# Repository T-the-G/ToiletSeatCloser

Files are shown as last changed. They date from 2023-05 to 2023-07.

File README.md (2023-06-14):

# Toilet Seat Closer

<figure>
  Timelapse of the toilet seat closer, the entire action takes about 2.5 minutes
</figure>
Lever that closes the toilet seat 

# Table of Contents  

- [Gallery](#gallery)
- [How it works](#how-it-works)
- [Bill of Materials](#bill-of-materials)  
  - [3D-printed parts](#3d-printed-parts)  
  - [Electronics](#electronics)
  - [Fasteners and other mechanical parts](#fasteners-and-other-mechanical-parts)
- [Future improvements](#future-improvements)

# Gallery

<p float="left">
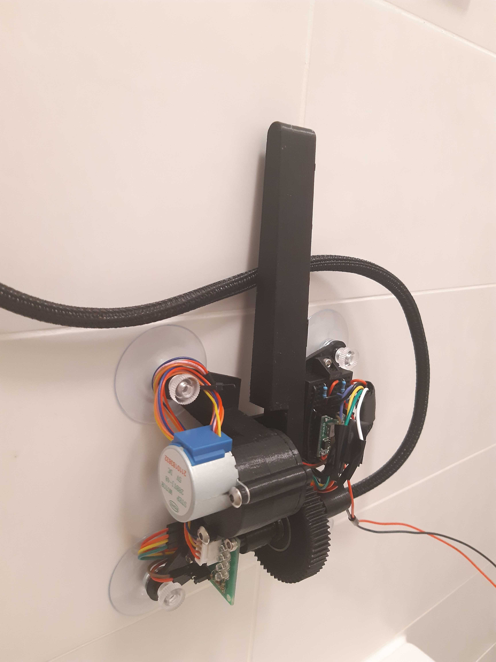
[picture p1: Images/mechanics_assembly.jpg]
  
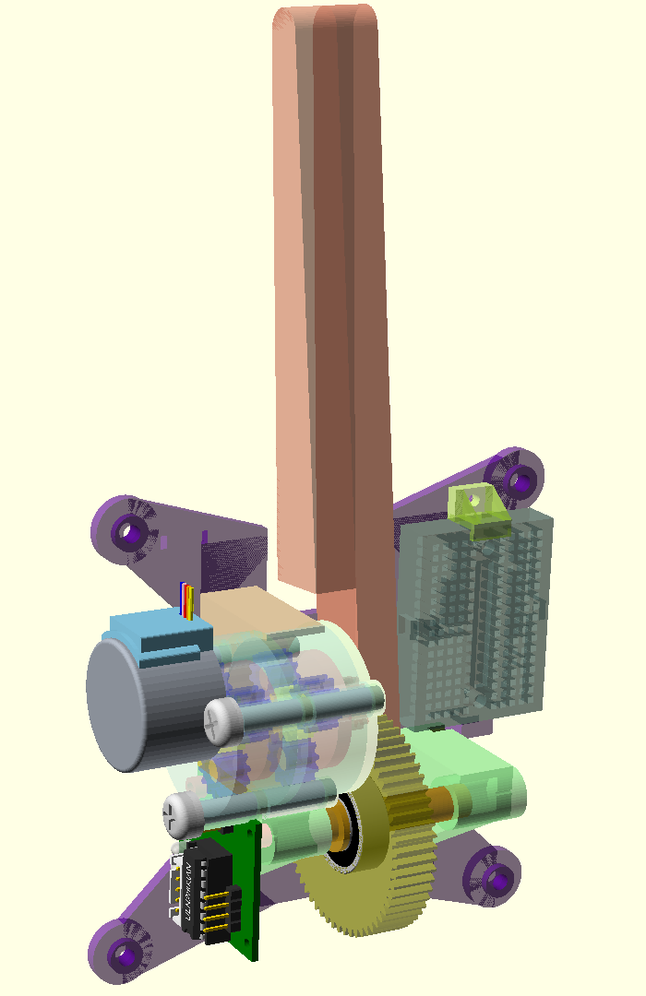
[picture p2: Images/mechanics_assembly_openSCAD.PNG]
   
</p>
Mechanics assembly

---

<p float="left">
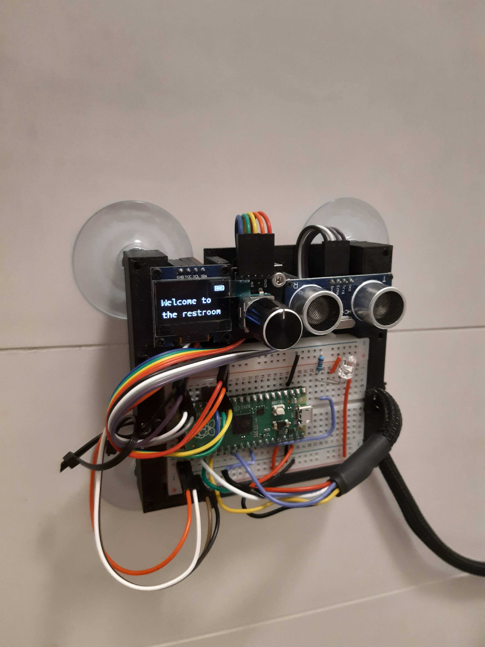
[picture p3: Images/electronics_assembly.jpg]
  
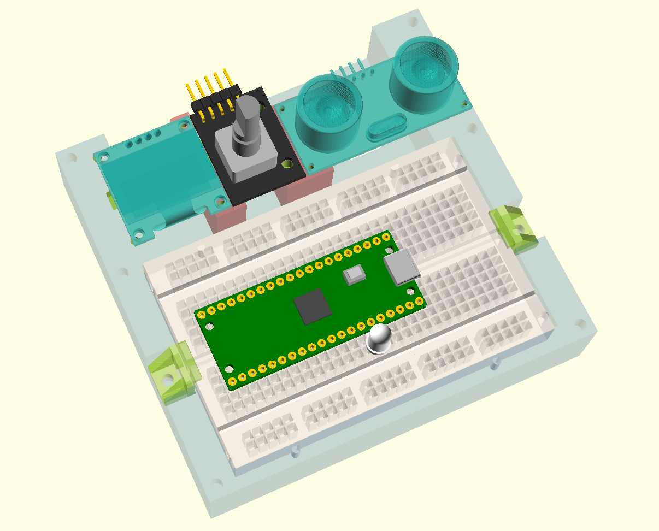
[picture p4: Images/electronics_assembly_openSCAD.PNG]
   
</p>
Electronics assembly

---

<p float="left">
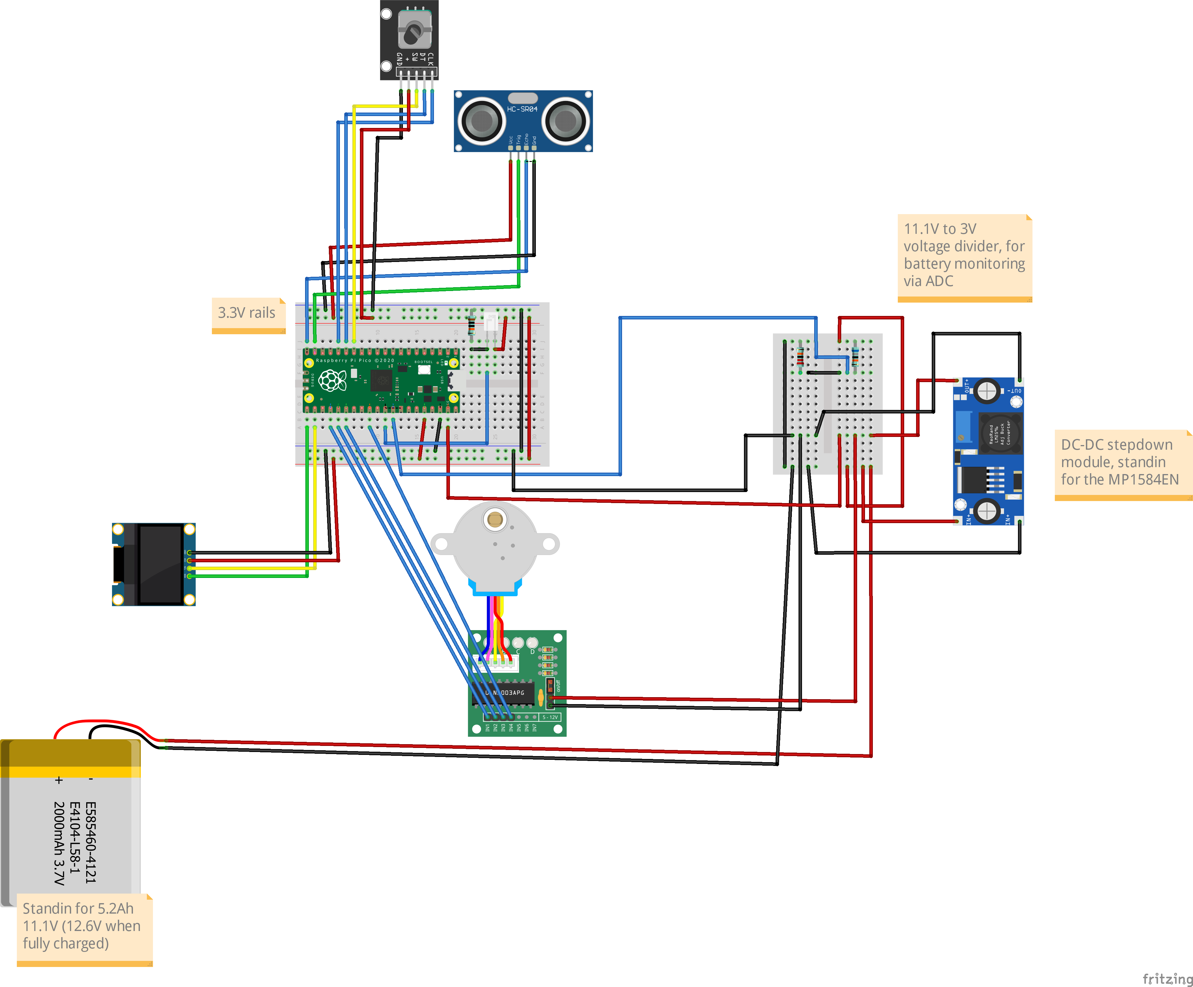
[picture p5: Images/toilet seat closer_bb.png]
  
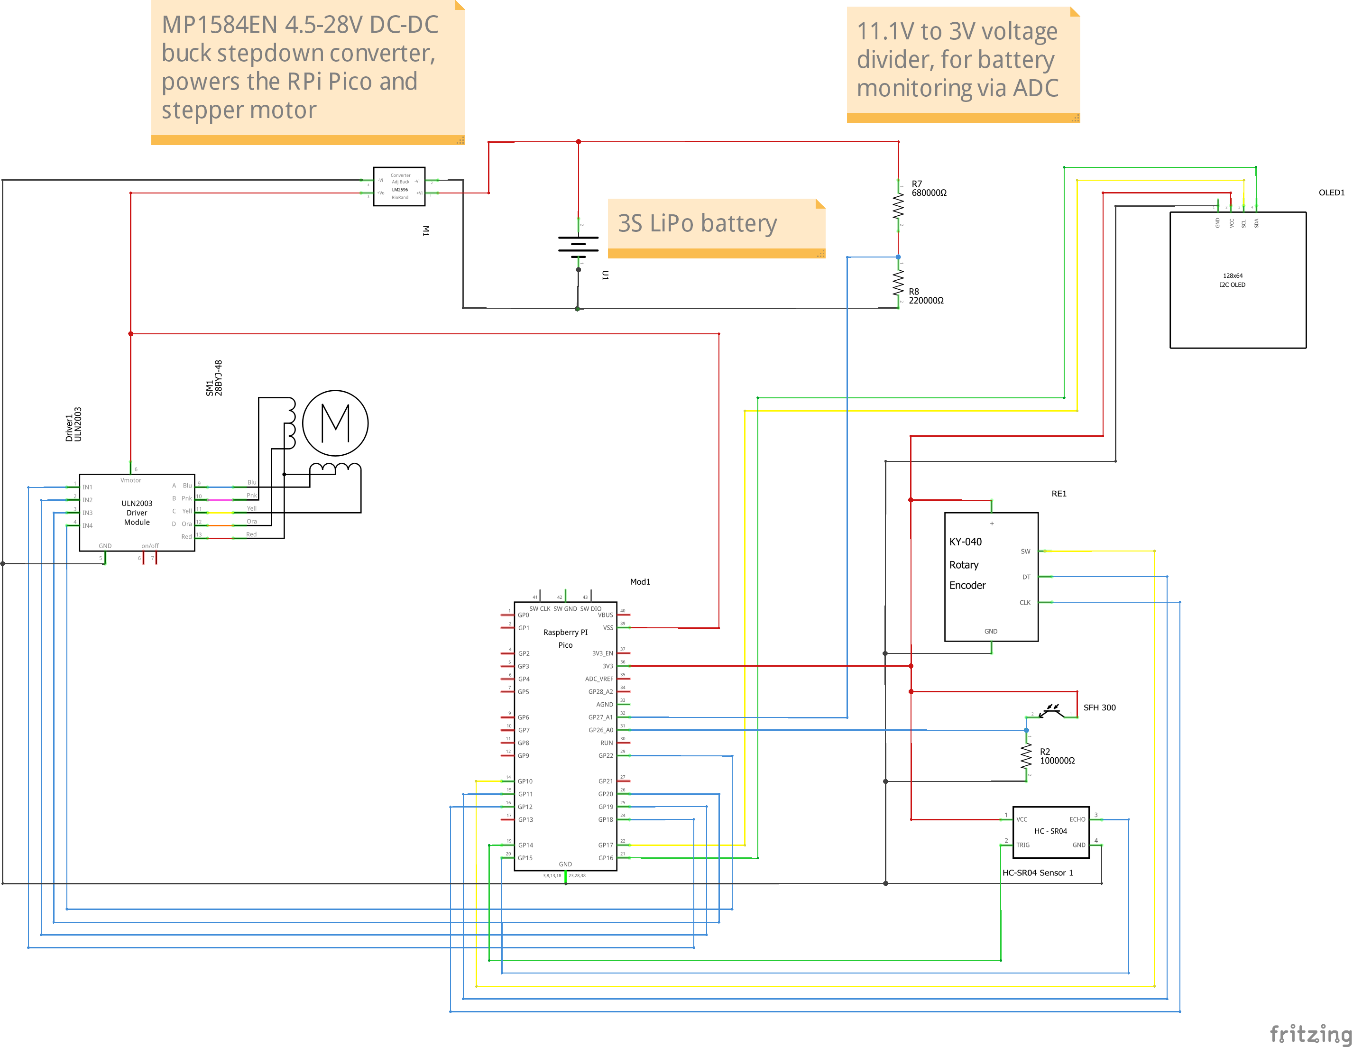
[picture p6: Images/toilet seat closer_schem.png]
   
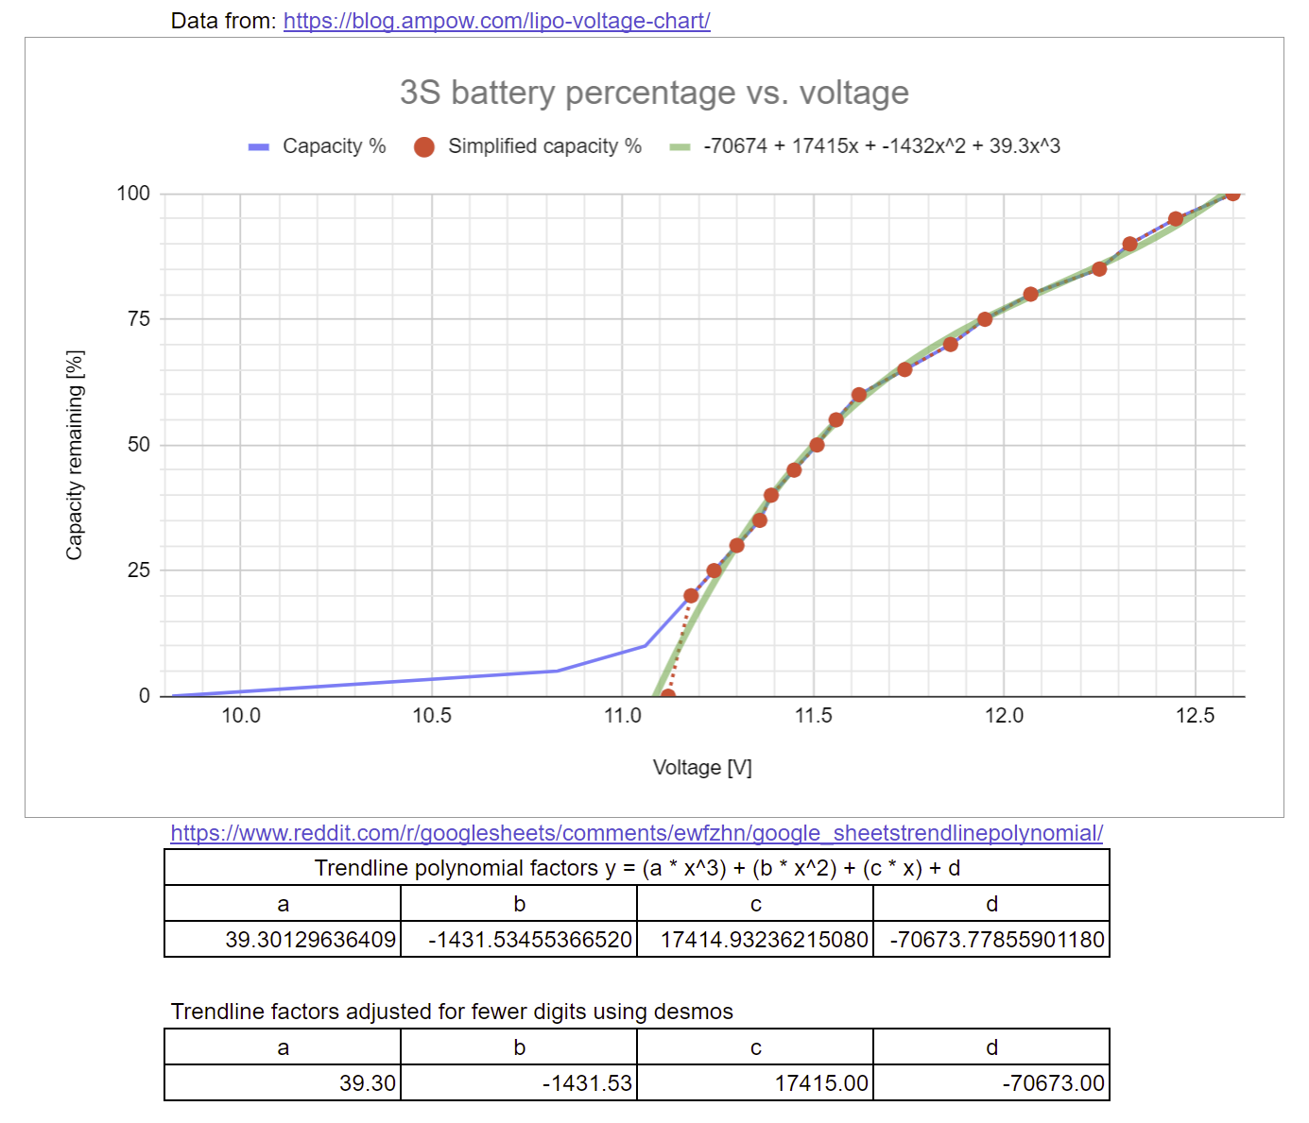
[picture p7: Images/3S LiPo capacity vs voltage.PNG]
  
</p>
Electronics diagrams

---

<figure>
    The oled screen when cycling between the three modes; AUTO, MANUAL, and DEBUG
</figure>
Oled display in action

# How it works

There are 3 modes which can be cycled through by pressing the rotary encoder button; AUTO, MANUAL, and DEBUG. When powering up the system by connecting to a battery, it goes into AUTO mode. 

###### AUTO mode
In AUTO mode, a light sensor and a distance sensor are used to determine presence in the restroom. Some time after presence is no longer detected (`action_after_seconds`), the lever actuates, and the toilet lid is closed. If presence is detected or the button is pushed during the action, the lever will begin retracting immediately.

###### MANUAL mode
Pressing the button while in AUTO mode switches the system to MANUAL mode, which immediately closes the lid, ignoring presence detection. If the MANUAL action completes without having pressed the button again, the system reverts to AUTO mode.

###### DEBUG mode
Pressing the button while in MANUAL mode switches the system to DEBUG mode, where sensor output is shown, and the motor can be actuated manually using the rotary encoder. This mode is useful for calibrating the variables `brightness_threshold`, `motion_threshold`, and `previous_distance`, as well as setting the lever's starting position. When switching from MANUAL to DEBUG mode, the motor will begin retracting the lever back to the starting position. This automatic retraction can be cancelled by turning the rotary encoder. If the button is pushed while the motor is off, or presence is not detected for `action_after_seconds`, the system switches to AUTO mode.

# Bill of Materials

This bill of materials is based on components I had lying around. It is perfectly possible to use different components. For example, one could use a photoresistor instead of a phototransistor, or a voltage regulator module instead of the DC-DC stepdown converter (or power the whole thing from a USB power supply plugged into the wall).

## 3D-printed parts

| Item | Quantity  |
| :--- | :---- |
| Axle | 1 |
| Backplate | 1 |
| Breadboard mounting bracket | 3 |
| Electronics backplate | 1 |
| Gearbox cover | 1 |
| m4 standoff 2.8mm | 2 |
| m4 standoff 3.2mm | 1 |
| Main gear and arm | 1 |
| Planet carrier | 2 |
| Planet gear | 6 |
| Rear axle mount | 1 |
| Ring gear base | 1 |
| Ring gear and front axle mount | 1 |
| Sun gear | 1 |

## Electronics

| Item | Quantity  | Description | 
| :--- | :---- | :--- |
| RaspberryPi Pico | 1 | Controlls the device  |
| 28BYJ-48 stepper motor | 1 | Actuates the arm |
| ULN2003 based driver board  | 1 | For driving the 28BYJ stepper motor |
| SFH 300 phototransistor | 1 | For detecting the ambient light level |
| HC-SR04 ultrasonic distance sensor  | 1 | For detecting movement |
| KY-040 rotary encoder | 1 | For manual control of the system |
| SSD1306 OLED display | 1 | Displays information about the device status, 0.96 inch, 128 x 64 resolution |
| 3S LiPo battery | 1 | Rated at 52Ah @ 11.1V (57.72Wh) |
| LiPo battery charger | 1 | Used to charge the LiPo battery |
| MP1584EN DC-DC buck module  | 1 | Provides steady voltage for the RPi Pico and the stepper motor, input 4.5-28V, output 0.8-20V 3A |
| Mini breadboard | 1 | Used as a power supply, has 170 pinholes, measures approximately 46\*35\*9mm |
| Small breadboard | 1 | Used as a motherboard, has 400 pinholes, measures approximately 82\*54\*9mm |
| 22AWG wires | 1 | For connecting components on the breadboards |
| Breadboard pin headers | 4 | For connecting the MP1584EN DC-DC stepdown module to the mini breadboard |
| 680KΩ resistor | 1 | Used in the 11.1V-to-3V voltage divider |
| 220KΩ resistor | 1 | Used in the 11.1V-to-3V voltage divider |
| 100KΩ resistor | 1 | Used for the SFH 300 phototransistor |
| T-plug or Deans connector | 1 | For connecting the battery to the mini breadboard |

## Fasteners and other mechanical parts

Note that the screw hole position/diameter on electronic components may vary between manufacturers. The relevant modifications can be made in front_axle_mount.scad (for the ULN2003 based driver board), and in electronics_backplate.scad (for the remaining components).

| Item | Quantity  | Description | 
| :--- | :---- | :--- |
| Suction cup | 8 | For attaching the backplates to a wall, 4cm diameter, M4\*10 thread  |
| M4\*35 | 3 | For holding the 28BYJ stepper motor and epicyclic gearbox in place  |
| M3 washer | 12 | To spread the load of the m3 screws on the backplate |
| M3\*25 | 4 | For connecting the front and rear axle mounts to the backplate |
| M3\*18 | 4 | For connecting the epicyclic ring gear base to the backplate |
| M3\*16 | 4 | For connecting the front and rear axle mounts to the backplate |
| M3\*6 | 3 | For connecting the breadboards to the backplates via the mounting brackets |
| M3\*4 | 5 | For mounting the ULN2003 driver board and KY-040 rotary encoder |
| M2\*4 | 4 | For mounting the SSD1300 OLED display to the electronics backplate  |
| M1.4\*6 | 4 | For mounting the HC-SR04 ultrasonic distance sensor to the electronics backplate |
| Spring | 1 | For pushing the axle back into place after manual adjustment, diameter 7mm, length 12.5mm |
| Cable sleeve  | 1 | Woven sheath that wraps around a 5-10mm bundle of cables, length approximately 70cm |
| 608RS bearing | 1 | Deep groove ball bearing which sits between the main gear and axle, bore diameter 8mm, external diameter 22mm, width 7mm |
| Lubricant | 1 | For the epicyclic gearbox |

# Future improvements

- Use a more powerful motor, such as the NEMA 23, for faster movement
- Use something cooler (and with less friction) than a two-stage planetary gear, such as a cycloidal drive, radial vector reducer, or split-ring compound planetary gear
- Use prototyping boards instead of breadboards, for better cable management
- Add a suction cup to the lever, to allow it to pull the lid back up, thus leaving only the seat down
- Use KiCad instead of Fritzing for the electronics diagrams
- Use the `uasyncio` library for a cleaner `main()` control loop

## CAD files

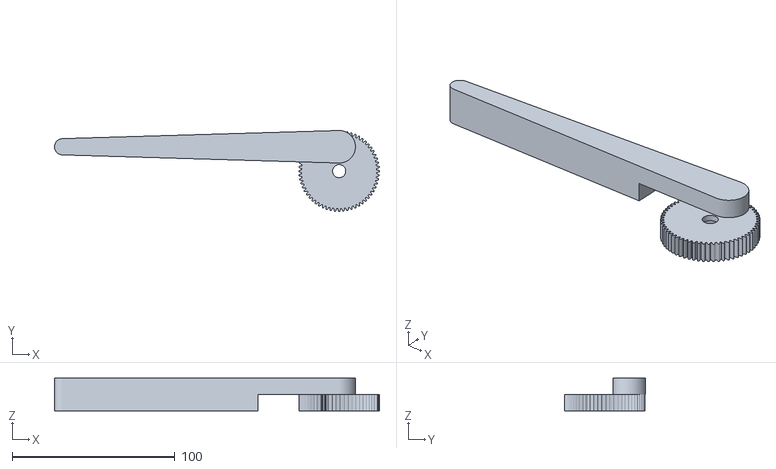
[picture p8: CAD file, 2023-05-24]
OpenSCAD/main_gear_and_arm.stl
199.8 x 49.8 x 20.0

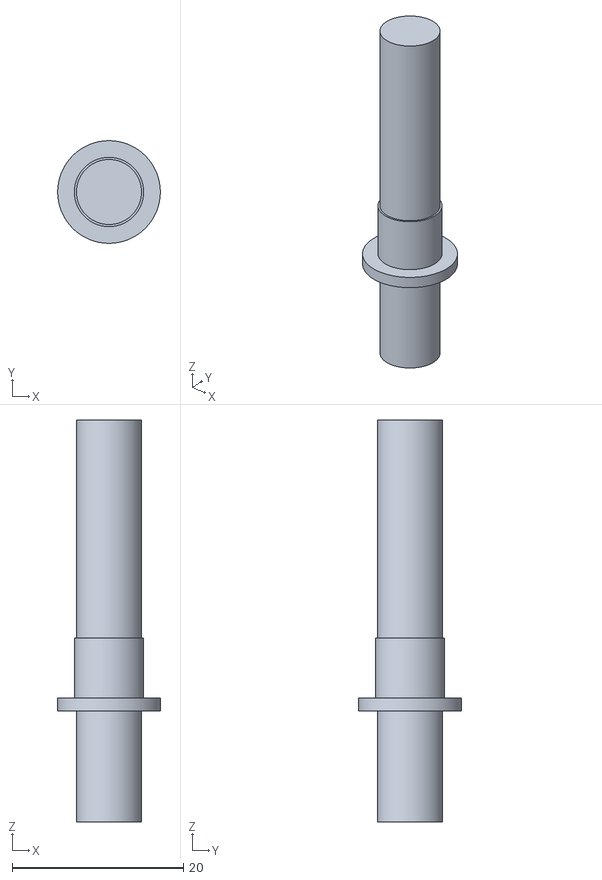
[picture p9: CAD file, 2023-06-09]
OpenSCAD/axle.stl
12.0 x 12.0 x 47.0

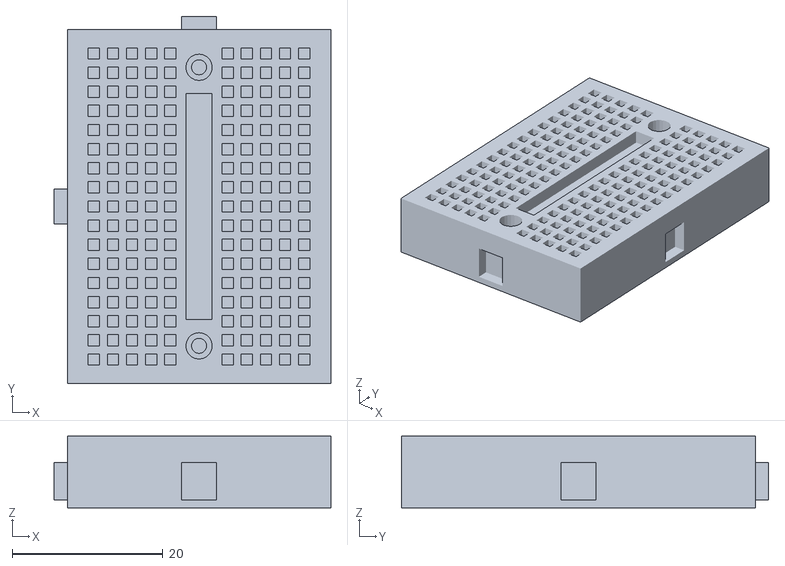
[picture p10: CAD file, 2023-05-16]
OpenSCAD/Breadboard/Mini_Breadboard.stl
36.7 x 48.8 x 9.50

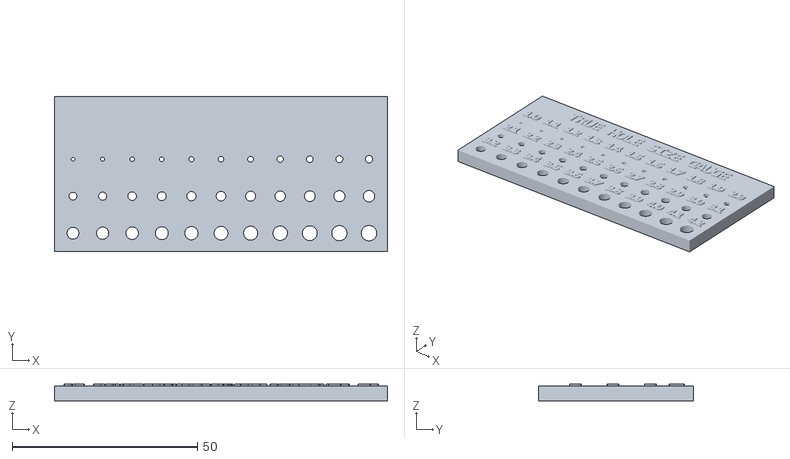
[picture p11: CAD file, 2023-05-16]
OpenSCAD/Test/Hole_Size_Gauge.STL
90.0 x 42.0 x 4.50

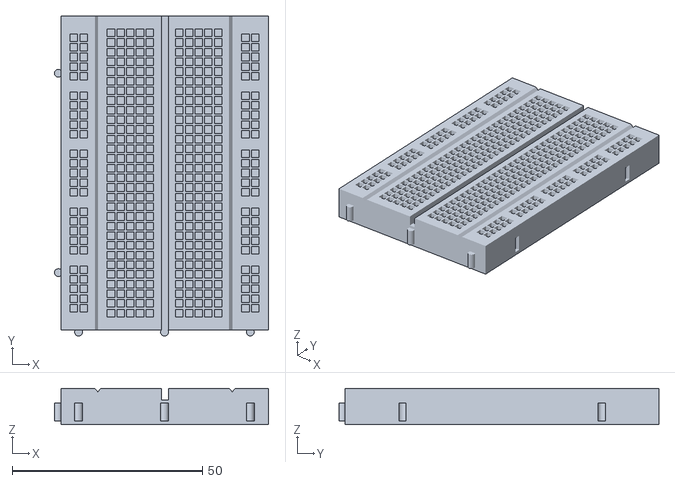
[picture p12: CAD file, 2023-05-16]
OpenSCAD/Breadboard/Small_Breadboard.stl
56.3 x 84.1 x 9.50

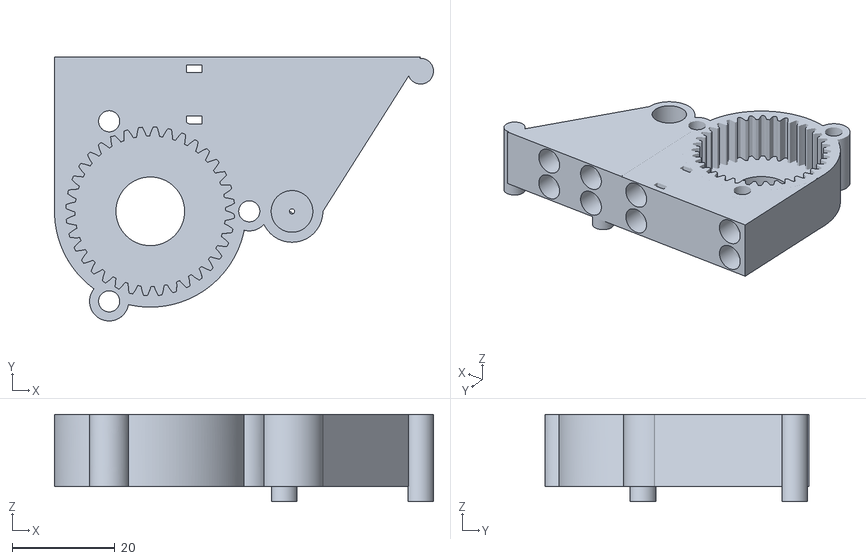
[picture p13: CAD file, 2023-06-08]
OpenSCAD/ring_gear_and_front_axle_mount.stl
73.7 x 51.3 x 17.0

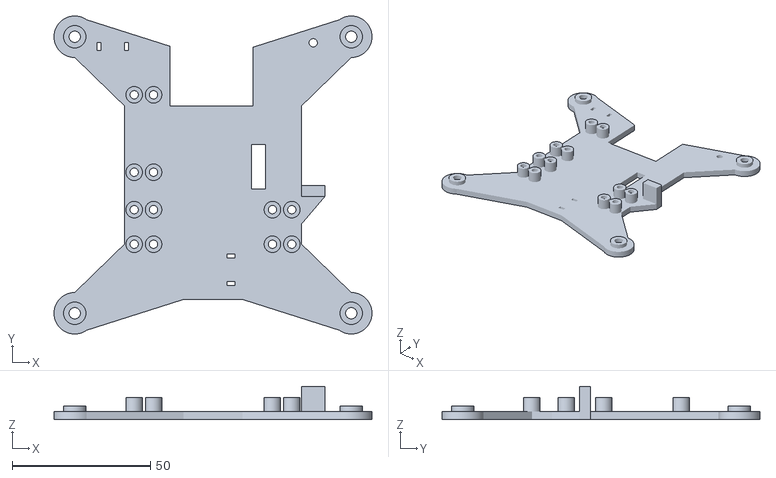
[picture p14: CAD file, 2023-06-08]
OpenSCAD/backplate.stl
115.0 x 115.0 x 12.0

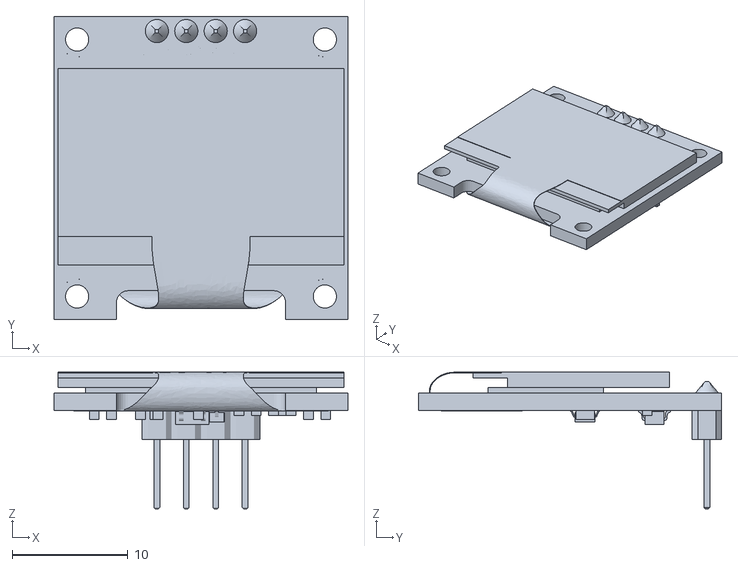
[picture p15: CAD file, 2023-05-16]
OpenSCAD/Breadboard/SSD1306_OLED_Display(128x64).stl
25.4 x 26.2 x 11.8

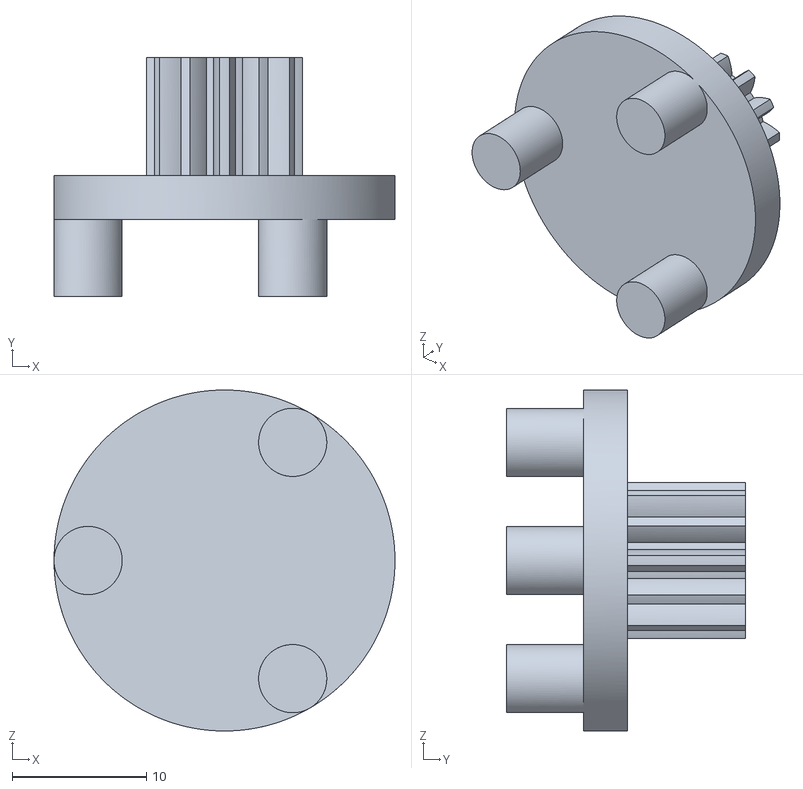
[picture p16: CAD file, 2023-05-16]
OpenSCAD/Planetary_Gearbox_for_the_28BYJ-48_Stepper_Motor/Planet_Carrier.stl
25.4 x 17.8 x 25.4

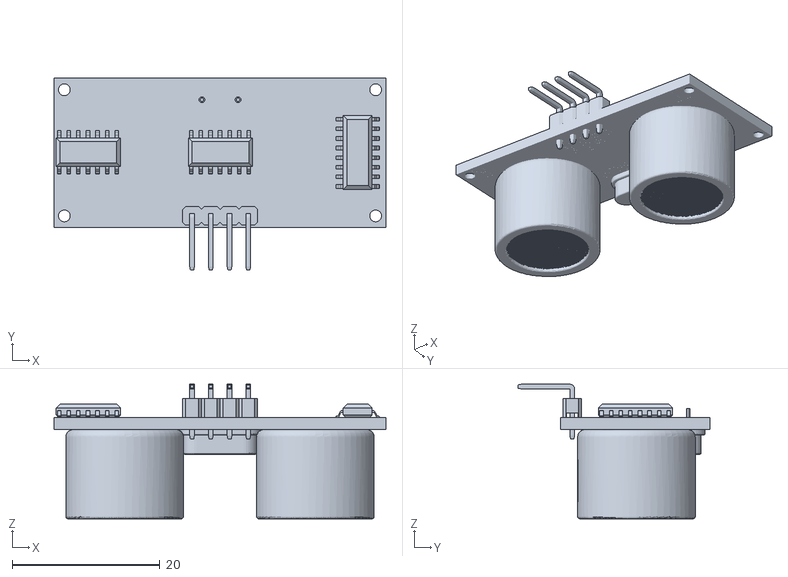
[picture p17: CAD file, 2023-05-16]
OpenSCAD/Breadboard/HC-SR04.stl
45.0 x 26.0 x 18.3

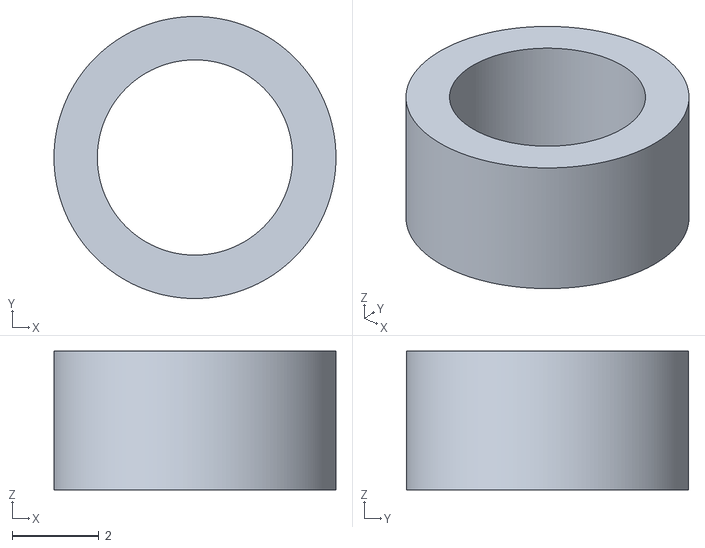
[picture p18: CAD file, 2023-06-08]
OpenSCAD/m4_standoff_3.2mm.stl
6.50 x 6.50 x 3.20

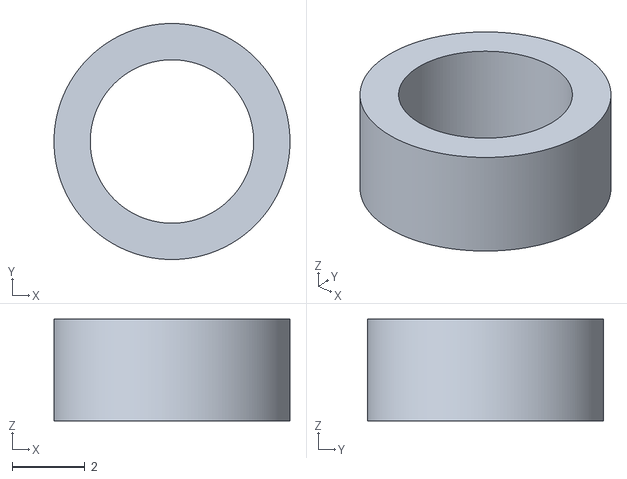
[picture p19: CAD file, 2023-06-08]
OpenSCAD/m4_standoff_2.8mm.stl
6.50 x 6.50 x 2.80

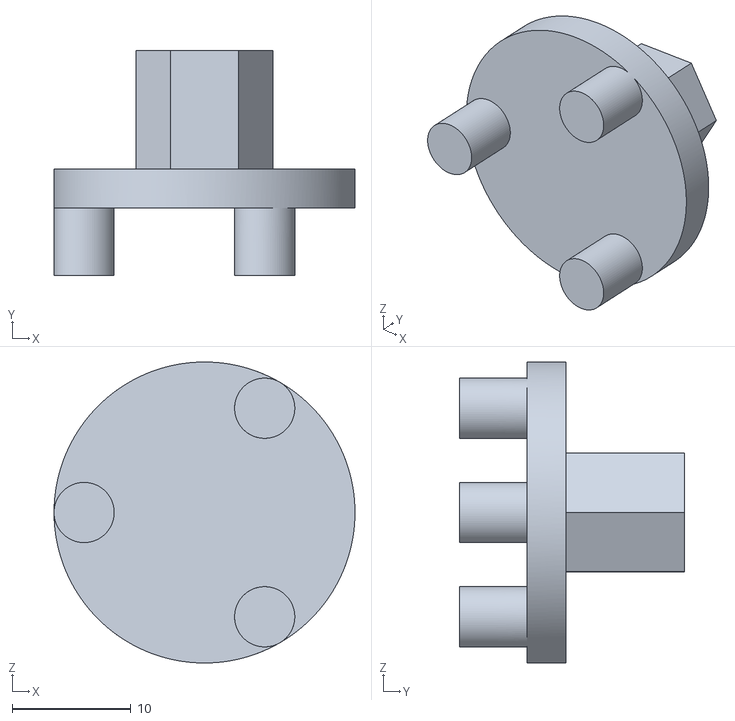
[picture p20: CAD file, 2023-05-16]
OpenSCAD/Planetary_Gearbox_for_the_28BYJ-48_Stepper_Motor/Planet_Carrier_10mm_Hex.stl
25.4 x 19.0 x 25.4

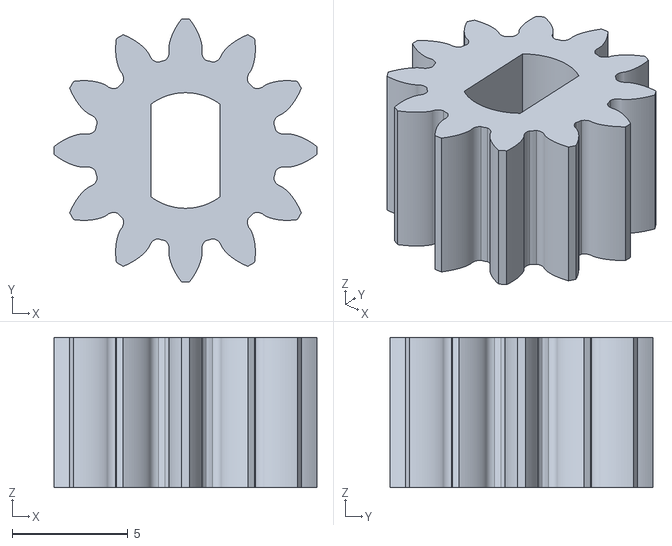
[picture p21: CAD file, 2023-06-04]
OpenSCAD/sun_gear.stl
11.4 x 11.4 x 6.50

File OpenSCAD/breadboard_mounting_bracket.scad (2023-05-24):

m3_hole_radius=1.5;

module mini_breadboard_mounting_bracket(breadboard_thickness=9, overhang=2) {
    color("YellowGreen",0.5)
    difference() {
        union() {
            // base
            cube([10,8,3]);
            // wall
            cube([10,2,breadboard_thickness+2]);
            // lip
            translate([0,-overhang,breadboard_thickness]) cube([10,overhang,2]);
            // support walls
            points=[[-6,0],[0,0],[0,breadboard_thickness+2-3]];
            translate([2,2,3]) rotate(a=-90, v=[0,0,1]) rotate(a=90, v=[1,0,0]) 
                linear_extrude(2, center=false, convexity=4) polygon(points);
            translate([10,2,3]) rotate(a=-90, v=[0,0,1]) rotate(a=90, v=[1,0,0]) 
                linear_extrude(2, center=false, convexity=4) polygon(points);
        }
        // m3 screw hole
        translate([5,5,-0.5]) cylinder(h=4, r=m3_hole_radius);
        // cutout for the breadboard knob/protrusion thing
        translate([5-4.5/2,-0.05,-1]) cube([4.5,2.1,6.5+1]);
    }
}
//cube([4.5,2,5.5]);







mini_breadboard_mounting_bracket();
//translate([0,-29,0]) import("Breadboard/Mini_Breadboard.stl", convexity=4);

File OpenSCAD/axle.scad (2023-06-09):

module axle_old() {
    color("DarkGoldenrod",0.7) union() {
        // main body
        cylinder(h=47, r=4);
        // spacer
        translate([0,0,12+1]) cylinder(h=1.5, r=6);
    }
}

module axle() {
    color("DarkGoldenrod",0.7) union() {
        // main body
        cylinder(h=47, r=4-0.2);
        // spacer
        translate([0,0,12+1]) cylinder(h=1.5, r=6);
        // friction fit onto bearing
        translate([0,0,14.5]) cylinder(h=7, r=4.05);
    }
}

axle();

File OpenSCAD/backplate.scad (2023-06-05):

// Mounting holes are 10cm apart along X and Y
mounting_holes_x_distance=100;
mounting_holes_y_distance=100;

// Mounting hole radii
m4_hole_radius=2.05;
m3_hole_radius=1.5;
mount_support_radius=m3_hole_radius+1.5;

// Height above backplate of supporting holes for the axle mounts and the ring gear base mount
mount_support_height=5;

// Height of screw holes for the suction cups
mounting_hole_height=5;

// Curvature of the ends of the mounting protrusions
mounting_web_radius=7.5;

backplate_thickness=3;
backplate_width=64;
backplate_height=90;

// Variables from full_assembly.scad
distance_between_gears=29.0385-1.5;
gearbox_z_offset=60;
gearbox_x_offset=0;

// Variables from front_axle_mount.scad
axle_mount_thickness=14;
root_height=25;

// Mounting protrusion
module mounting_web() {
    difference() {
        union() {
            // round tip of the mounting protrusion
            cylinder(h=backplate_thickness, r=mounting_web_radius);
            // extra height for the screw hole
            cylinder(h=mounting_hole_height, r=m4_hole_radius+2);
            // polygon which forms the web (connects the tip to the main rectangle)
            linear_extrude(backplate_thickness, center = false, convexity = 4) {
                // polygon points
                p1=[0,-mounting_web_radius];
                p2=[backplate_width/3-backplate_width/2+mounting_holes_x_distance/2,
                    -backplate_height/2+mounting_holes_y_distance/2];
                p3=[-backplate_width/2+mounting_holes_x_distance/2,
                    backplate_height/3+backplate_height/2-mounting_holes_y_distance/2];
                p4=[0,mounting_web_radius];
                polygon([p1,p2,p3,p4]);
            }
        }
        // cutout for the mounting hole
        translate([0,0,-0.5]) cylinder(h=mounting_hole_height+1, r=m4_hole_radius);
    }
}
//translate([backplate_width/2-mounting_holes_x_distance/2,backplate_height/2-mounting_holes_y_distance/2,0]) mounting_web();

module m3_hole_support() {
    color("Crimson", 0.9)
    difference() {
        // main body
        cylinder(h=backplate_thickness+mount_support_height, r=mount_support_radius);
        // cutout m3 hole
        translate([0,0,-0.5]) cylinder(h=backplate_thickness+5+1, r=m3_hole_radius);
    }
}
//m3_hole_support();

module axle_mount_hole_supports() {
    translate([axle_mount_thickness/4,0,0]) m3_hole_support();
    translate([axle_mount_thickness*3/4,0,0]) m3_hole_support();
    translate([axle_mount_thickness/4,root_height/2,0]) m3_hole_support();
    translate([axle_mount_thickness*3/4,root_height/2,0]) m3_hole_support();
}
//axle_mount_hole_supports();

module axle_mount_holes() {
    translate([axle_mount_thickness/4,0,-0.5]) cylinder(h=backplate_thickness+1, r=m3_hole_radius);
    translate([axle_mount_thickness*3/4,0,-0.5]) cylinder(h=backplate_thickness+1, r=m3_hole_radius);
    translate([axle_mount_thickness/4,root_height/2,-0.5]) cylinder(h=backplate_thickness+1, r=m3_hole_radius);
    translate([axle_mount_thickness*3/4,root_height/2,-0.5]) cylinder(h=backplate_thickness+1, r=m3_hole_radius);
}
//axle_mount_holes();

module ring_gear_base_mount_hole_supports() {
    translate([14/4,14,0]) m3_hole_support();
    translate([14/4,-14,0]) m3_hole_support();
    translate([14*3/4,14,0]) m3_hole_support();
    translate([14*3/4,-14,0]) m3_hole_support();
}
//ring_gear_base_mount_hole_supports();

module ring_gear_base_mount_holes() {
    translate([14/4,14,-0.5]) cylinder(h=backplate_thickness+1, r=m3_hole_radius);
    translate([14/4,-14,-0.5]) cylinder(h=backplate_thickness+1, r=m3_hole_radius);
    translate([14*3/4,14,-0.5]) cylinder(h=backplate_thickness+1, r=m3_hole_radius);
    translate([14*3/4,-14,-0.5]) cylinder(h=backplate_thickness+1, r=m3_hole_radius);
}
//ring_gear_base_mount_holes();

module backplate() {
    color("Indigo",0.6) 
    difference() {
        union() {
            // 4 mounting webs
            translate([backplate_width/2-mounting_holes_x_distance/2,backplate_height/2-mounting_holes_y_distance/2,0])
                mounting_web();
            translate([backplate_width/2+mounting_holes_x_distance/2,backplate_height/2-mounting_holes_y_distance/2,0])
                mirror([1,0,0]) mounting_web();
            translate([backplate_width/2-mounting_holes_x_distance/2,backplate_height/2+mounting_holes_y_distance/2,0])
                mirror([0,1,0]) mounting_web();
            translate([backplate_width/2+mounting_holes_x_distance/2,backplate_height/2+mounting_holes_y_distance/2,0])
                mirror([0,1,0]) mirror([1,0,0]) mounting_web();
            // main rectangle
            cube([backplate_width,backplate_height,backplate_thickness]);
            // bottom latch for the power distribution mini-breadboard
            translate([backplate_width,30.7615+6+0.5,0]) 
            difference() {
                union() {
                    // main latch body
                    cube([8.5,4,9+backplate_thickness]);
                    // small triangular support
                    linear_extrude(backplate_thickness, center = false, convexity = 4) {
                        points=[[8.5,0],[0,-10],[0,0]];
                        polygon(points);
                    }
                }
                // square hole cutout to hold the mini-breadboard by the notch
                translate([8.5/4,2.01,backplate_thickness+0.75]) cube([4.5,2,6]);
            }
            // m3 mounting supports for front axle mount
            translate([gearbox_x_offset+0,gearbox_z_offset-distance_between_gears-root_height/2,0]) 
                axle_mount_hole_supports();
            // m3 mounting supports for rear axle mount
            translate([gearbox_x_offset+50,gearbox_z_offset-distance_between_gears-root_height/2,0]) 
                axle_mount_hole_supports();
            // m3 mounting supports for the ring gear base mount (gearbox)
            translate([gearbox_x_offset,gearbox_z_offset,0]) 
                ring_gear_base_mount_hole_supports();
        }
        // hole for the power cables from the battery, and for the 6 wires going to the stepper driver board
        translate([backplate_width-12-6,40,-0.5]) cube([5,16,backplate_height+1]);
        // parallel holes for ziptie cable management on top left web
        translate([-10,backplate_height-0,-0.5]) cube([1.5,3,backplate_thickness+1]);
        translate([0,backplate_height-0,-0.5]) cube([1.5,3,backplate_thickness+1]);
        // parallel holes for ziptie cable management in bottom center
        translate([backplate_width/2+5,15,-0.5]) cube([3,1.5,backplate_thickness+1]);
        translate([backplate_width/2+5,5,-0.5]) cube([3,1.5,backplate_thickness+1]);
        // m3 mounting holes for front axle mount
        translate([gearbox_x_offset+0,gearbox_z_offset-distance_between_gears-root_height/2,0]) 
            axle_mount_holes();
        // m3 mounting holes for rear axle mount
        translate([gearbox_x_offset+50,gearbox_z_offset-distance_between_gears-root_height/2,0])
            axle_mount_holes();
        // m3 mounting holes for the ring gear base mount (gearbox)
        translate([gearbox_x_offset,gearbox_z_offset,0]) 
            ring_gear_base_mount_holes();
        // m3 mounting hole for the mini-breadboard mounting bracket
        translate([64-(10-8.5)/2+5, 41.3+46.5+5, -0.5])
            cylinder(h=backplate_thickness+1, r=m3_hole_radius);
        // cutout for the main arm, so it can swing back beyond 3 degrees
        translate([18.5-2, backplate_height-20, -0.5]) cube([30,30,backplate_thickness+1]);
        
    }
}

backplate();







// Guides for the mounting holes
/*
translate([backplate_width/2-mounting_holes_x_distance/2,backplate_height/2-mounting_holes_y_distance/2,0]) 
    cylinder(h=backplate_thickness, r=m4_hole_radius);
translate([backplate_width/2+mounting_holes_x_distance/2,backplate_height/2-mounting_holes_y_distance/2,0]) 
    cylinder(h=backplate_thickness, r=m4_hole_radius);
translate([backplate_width/2-mounting_holes_x_distance/2,backplate_height/2+mounting_holes_y_distance/2,0]) 
    cylinder(h=backplate_thickness, r=m4_hole_radius);
translate([backplate_width/2+mounting_holes_x_distance/2,backplate_height/2+mounting_holes_y_distance/2,0]) 
    cylinder(h=backplate_thickness, r=m4_hole_radius);
*/

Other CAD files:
OpenSCAD/planet_gear.stl
OpenSCAD/gearbox_cover.stl
OpenSCAD/ring_gear_base.stl
OpenSCAD/rear_axle_mount.stl
OpenSCAD/electronics_backplate.scad
OpenSCAD/Planetary_Gearbox_for_the_28BYJ-48_Stepper_Motor/Gearbox_Cover.stl
OpenSCAD/Planetary_Gearbox_for_the_28BYJ-48_Stepper_Motor/Planet_Gear.stl
OpenSCAD/Planetary_Gearbox_for_the_28BYJ-48_Stepper_Motor/Ring_Gear_Base.stl
OpenSCAD/Planetary_Gearbox_for_the_28BYJ-48_Stepper_Motor/Sun_Gear.stl
OpenSCAD/Test/test_electronics_mounting.scad
OpenSCAD/Test/test_hole_size.scad
OpenSCAD/breadboard_mounting_bracket.stl
OpenSCAD/electronics_backplate.stl
OpenSCAD/electronics_subassembly.scad
OpenSCAD/epicyclic_gear_subassembly.scad
OpenSCAD/front_axle_mount.scad
OpenSCAD/full_assembly.scad
OpenSCAD/gears.scad
OpenSCAD/generate_stl_files.scad
OpenSCAD/main_gear.scad
OpenSCAD/rear_axle_mount.scad
OpenSCAD/ring_gear_and_front_axle_mount.scad
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

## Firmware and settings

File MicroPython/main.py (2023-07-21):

# Using firmware rp2-pico-20230414-unstable-v1.19.1-1016-gb525f1c9e.uf2 
from machine import Pin, I2C, ADC
import utime
import math
import _thread
import micropython
import gc
gc.enable()
# SSD1306 OLED display, install the following modules from PyPI:
# micropython-ssd1306 v0.3 by Stefan Lehmann
# micropython-oled v1.13 by Yeison Cardona 
from ssd1306 import SSD1306_I2C, framebuf
from oled import Write
from oled.fonts import ubuntu_mono_20, ubuntu_mono_15, ubuntu_condensed_12

####################################
# Variables that need calibration #
####################################
action_after_seconds        = micropython.const(600)    # seconds to wait after presence is no longer detected to close the lid or revert to AUTO mode
action_revolutions          = micropython.const(17)     # stepper motor rotations required to close the toilet lid
brightness_threshold        = micropython.const(10)     # phototransistor brightness (%) threshold for detecting restroom light
motion_threshold            = micropython.const(5)      # difference in distance (cm) between successive measurements to detect motion 
oled_dim                    = micropython.const(100)    # value between 0 (dimmest) and 255 (brightest) to dim the oled display
polling_interval_debug      = micropython.const(0.25)   # seconds between polling (and screen refresh) when in DEBUG mode
polling_interval_presence   = micropython.const(1)      # seconds between polling when presence has been detected
polling_interval_standby    = micropython.const(5)      # seconds between polling during standby
previous_distance           = micropython.const(50)     # initialise typical distance (cm) measured when nobody is in the restroom
step_sleep_close            = micropython.const(0.0025) # seconds between stepper motor steps during lid close action
step_sleep_retract          = micropython.const(0.002)  # seconds between stepper motor steps during retract action
# 3S battery produces 12.6V when fully charged. Voltage divider equation: Vout = Vin * R2 / (R1 + R2)
# R1 = 680KOhm, R2 = 220KOhm, so 12.6Vin give 3.08Vout
# read_u16() returns a 16bit unsigned integer (between 0 and 65535, at 0V and 3.3V respectively)
# original voltage Vin = read_u16() * 12.6/65535 * 3.3/3.08
# another way to calculate original voltage = read_u16() * 3.3/65535 * (R1 + R2)/R2
voltage_conversion_factor   = micropython.const(3.3/65535 * (680+220)/220)
voltage_correction_factor   = micropython.const(0.50)   # my maths is flawless but my hardware is not; set this to zero, hook everything up, measure voltage with a multimeter and with the ADC (example: 11.97 and 11.47), the difference is the correction factor

###################
#   Define pins   #
###################
# SSD1306 OLED I2C
pin_oled_sda        = Pin(16)
pin_oled_scl        = Pin(17)
# KY-040 rotary encoder
pin_ky040_clk       = Pin(12, Pin.IN, Pin.PULL_DOWN)
pin_ky040_dt        = Pin(11, Pin.IN, Pin.PULL_DOWN)
pin_ky040_sw        = Pin(10, Pin.IN, Pin.PULL_DOWN)
# HC-SR04 ultrasonic distance sensor
pin_hcsr04_trigger  = Pin(14, Pin.OUT)
pin_hcsr04_echo     = Pin(15, Pin.IN)
# SFH 300 phototransistor
pin_sfh300_adc      = ADC(26)
# 3S LiPo battery
pin_battery_adc     = ADC(27)
# 28BYJ-48 stepper motor
pin_motor_1         = Pin(18, Pin.OUT)
pin_motor_2         = Pin(19, Pin.OUT)
pin_motor_3         = Pin(20, Pin.OUT)
#pin_motor_4         = Pin(21, Pin.OUT) # I somehow broke this pin
pin_motor_4         = Pin(22, Pin.OUT)

##########################################
# Glabal variables for the state machine #
##########################################
# Pushing the button cycles between three modes:
# AUTO:     poll sensors and close lid after presence is no longer detected
# MANUAL:   immediately close the lid, ignoring presence detection
# DEBUG:    manually adjust position, and display sensor output. Useful for calibration
action_in_progress  = False # true if the motor is being actuated
motor_cancel        = False # used to stop the motor if action is in progress
mode_debug          = False # true if DEBUG mode is engaged
mode_manual         = False # true if MAUNAL mode is engaged
mode_switch         = False # used in the main function to break out of loops


######################
#   Setup the OLED   #
######################
oled_width = micropython.const(128)
oled_height = micropython.const(64)
# the first argument of I2C is the set of i2c pins which should be initialised
i2c=I2C(0, scl=pin_oled_scl, sda=pin_oled_sda, freq=400000)
oled = SSD1306_I2C(oled_width, oled_height, i2c)
oled.contrast(oled_dim)
# fonts
write12 = Write(oled, ubuntu_condensed_12)
write15 = Write(oled, ubuntu_mono_15)
write20 = Write(oled, ubuntu_mono_20)

# Battery icons
class battery_status:
    _FONT = {
        49: [20, 1099511627775, 1099511627775, 1099511627775, 824633720832, 824633720832, 17179869168, 17179869168, 68719476720, 68719476720, 17179869168, 17179869168, 824633720832, 824633720832, 1099511627775],
        50: [20, 1099511627775, 1099511627775, 1099511627775, 824633720832, 824633720832, 17179869168, 17179852848, 68719460400, 68719460400, 17179852848, 17179869168, 824633720832, 824633720832, 1099511627775],
        51: [20, 1099511627775, 1099511627775, 1099511627775, 824633720832, 824633720832, 17179869168, 17178820656, 68718428208, 68718428208, 17178820656, 17179869168, 824633720832, 824633720832, 1099511627775],
        52: [20, 1099511627775, 1099511627775, 1099511627775, 824633720832, 824633720832, 17179869168, 17112760368, 68652367920, 68652367920, 17112760368, 17179869168, 824633720832, 824633720832, 1099511627775],
        53: [20, 1099511627775, 1099511627775, 1099511627775, 824633720832, 824633720832, 17179869168, 12884901936, 64424509488, 64424509488, 12884901936, 17179869168, 824633720832, 824633720832, 1099511627775],
        }
battery = Write(oled, battery_status)

# Lightbulb icon
class lightbulb_icon:
    _FONT = {
        'lightbulb': [11, 4128831, 3932175, 3146691, 3145779, 3145776, 3145731, 3145731, 3932163, 4128783, 4128831, 4194303, 4177983, 4177983, 4190463, 4194303],
        }
lightbulb = Write(oled, lightbulb_icon)

# Horizontal arrows icon (might look better than the ruler icon)
class horizontal_arrows_icon:
    _FONT = {
        'arrows-alt-h': [14, 268435455, 268435455, 268435455, 268435455, 265289535, 252706575, 201326595, 0, 201326592, 252706575, 265289535, 268435455, 268435455, 268435455, 268435455],
        }
arrows = Write(oled, horizontal_arrows_icon)

# Toilet icon (profile) shown when action is ongoing
toilet_icon_array = bytearray(b'\x00\x00\x00\x00\x00\x00\x00\x00\x00\x00\x00\x00\x00\x00\x00\x00\xe0\x00\x00\x00\x00\x00\x00\xa0\x00\x00\x00\x00\x00\x07\xfc\x00\x00\x00\x00\x00\x0c\x06\x00\x00\x00\x00\x00\x18\x02\x00\x00\x00\x00\x00\x10\x01\x00\x00\x00\x00\x00\x10\x01\x00\x00\x00\x00\x00\x10\x01\x00\x00\x00\x00\x00\x10\x01\x00\x00\x00\x00\x00\x10\x01\x00\x00\x00\x00\x00\x10\x01\x00\x00\x00\x00\x00\x10\x01\x00\x00\x00\x00\x00\x10\x01\x00\x00\x00\x00\x00\x10\x01\x00\x00\x00\x00\x00\x10\x01\x00\x00\x00\x00\x00\x10\x01\x00\x00\x00\x00\x00\x10\x01\x00\x00\x00\x00\x00\x10\x01\x00\x00\x00\x00\x00\x10\x01\x00\x00\x00\x00\x00\x10\x01\x00\x00\x00\x00\x00\x10\x01\x00\x00\x00\x00\x00\x10\x01\x00\x00\x00\x00\x00\x10\x01\x00\x00\x00\x00\x00\x10\x01\x00\x00\x00\x00\x00\x10\x01\xff\xff\xf8\x00\x00\x10\x01\x80\x00\x04\x00\x00\x1f\xff\xff\xff\xfc\x00\x00\x10\x00\x00\x00\x04\x00\x00\x10\x00\x00\x00\x04\x00\x00\x10\x00\x00\x00\x04\x00\x00\x08\x00\x00\x00\x08\x00\x00\x08\x00\x00\x00\x10\x00\x00\x04\x00\x00\x00`\x00\x00\x06\x00\x00\x01\x80\x00\x00\x02\x00\x00\x03\x00\x00\x00\x01\x00\x00\x04\x00\x00\x00\x00\x80\x00\x08\x00\x00\x00\x00@\x00\x18\x00\x00\x00\x00@\x00\x10\x00\x00\x00\x00 \x00\x10\x00\x00\x00\x00 \x00 \x00\x00\x00\x00 \x00 \x00\x00\x00\x00 \x00 \x00\x00\x00\x00`\x00 \x00\x00\x00\x00@\x00 \x00\x00\x00\x00@\x00\x10\x00\x00\x00\x00\xc0\x00\x10\x00\x00\x00\x00\x80\x00\x08\x00\x00\x00\x00\x80\x00\x08\x00\x00\x00\x00\xff\xff\xf0\x00\x00\x00\x00\x00\x00\x00\x00\x00\x00\x00\x00\x00\x00\x00\x00\x00\x00\x00\x00\x00\x00\x00')
toilet_icon = framebuf.FrameBuffer(toilet_icon_array, 55, 55, framebuf.MONO_HLSB)

###########################
# Setup the stepper motor #
###########################
steps_per_revolution = micropython.const(2048)      # stepper motor steps per revolution
motor_direction=True # True for clockwise (closing seat), False for counter-clockwise (retracting arm) (as seen when looking from the back of the motor)
motor_retract_revolutions = 0 # If the action is interrupted, reverse the motor by this amount of revolutions
step_sequence = [[1,0,0,0],
                 [0,1,0,0],
                 [0,0,1,0],
                 [0,0,0,1]]
motor_pins = [pin_motor_1, pin_motor_2, pin_motor_3, pin_motor_4]

############################
# Setup the rotary encoder #
############################
last_button_time    = 0 # last time the button was pushed
rotary_counter      = 0 # position of the knob, 20 steps per 360 degrees
last_rotation_time  = 0 # last time either dt or clk interrupt occured
deadzone            = micropython.const(math.radians(40))   # rotation deadzone, 18 degrees per step, so 40 degrees is about two steps in either direction
max_rotation_steps  = micropython.const(10)                 # limit how many steps in either direction can be made, 10 steps is half a rotation

#################
#   Functions   #
#################

def button_interrupt(pin):
    irq_state = machine.disable_irq()
    global motor_cancel, last_button_time, mode_debug, mode_manual, mode_switch
    # <debounce>
    new_button_time = utime.ticks_ms()
    if utime.ticks_diff(new_button_time, last_button_time) < 200:
        machine.enable_irq(irq_state)
        return
    else:
        last_button_time = new_button_time
    # </debounce>
    motor_cancel = True
    # switch from AUTO to MANUAL
    if not mode_debug and not mode_manual:
        mode_manual = True
        mode_switch = True
    # switch from MANUAL to DEBUG
    elif not mode_debug and mode_manual:
        mode_debug = True
        mode_manual = False
        mode_switch = True
    # switch from DEBUG to AUTO
    elif mode_debug and not mode_manual:
        mode_debug = False
        mode_switch = True
    # Defensive programming
    else:
        motor_cleanup()
        oled.fill(0)
        write12.text("State machine error", 0, 0)
        oled.show()
        print("State machine error")
        machine.enable_irq(irq_state)
        exit(1)
    machine.enable_irq(irq_state)

def clk_interrupt(pin):
    irq_state = machine.disable_irq()
    global motor_cancel, last_rotation_time, rotary_counter
    # only do something in DEBUG mode
    if not mode_debug:
        machine.enable_irq(irq_state)
        return
    # debounce
    new_rotation_time = utime.ticks_ms()
    if utime.ticks_diff(new_rotation_time, last_rotation_time) < 20:
        machine.enable_irq(irq_state)
        return
    else:
        last_rotation_time = new_rotation_time
    # immediately stop motor if retraction is in progress during debug mode
    if action_in_progress:
        motor_cancel = True
    # don't register more than half a rotation
    if rotary_counter >= max_rotation_steps:
        rotary_counter = max_rotation_steps
        machine.enable_irq(irq_state)
        return
    # Increment counter
    clk_state   = pin_ky040_clk.value()
    dt_state    = pin_ky040_dt.value()
    if clk_state == 0 and dt_state == 1:
        rotary_counter += 1
    machine.enable_irq(irq_state)

def dt_interrupt(pin):
    irq_state = machine.disable_irq()
    global motor_cancel, last_rotation_time, rotary_counter
    # only do something in DEBUG mode
    if not mode_debug:
        machine.enable_irq(irq_state)
        return
    # <debounce>
    new_rotation_time = utime.ticks_ms()
    if utime.ticks_diff(new_rotation_time, last_rotation_time) < 20:
        machine.enable_irq(irq_state)
        return
    else:
        last_rotation_time = new_rotation_time
    # immediately stop motor if retraction is in progress during debug mode
    if action_in_progress:
        motor_cancel = True
    # don't register more than half a rotation
    if rotary_counter <= -max_rotation_steps:
        rotary_counter = -max_rotation_steps
        machine.enable_irq(irq_state)
        return
    # Increment counter
    clk_state   = pin_ky040_clk.value()
    dt_state    = pin_ky040_dt.value()
    if clk_state == 1 and dt_state == 0:
        rotary_counter -= 1
    machine.enable_irq(irq_state)
        
def clear_screen():
    oled.fill(0)
    oled.show()

def detect_presence():
    global previous_distance
    brightness_detected = False
    motion_detected = False
    presence_detected = False
    brightness = measure_brightness()
    if brightness > brightness_threshold:
        brightness_detected = True
    distance = measure_distance()
    if distance > previous_distance + motion_threshold or distance < previous_distance - motion_threshold:
        motion_detected = True
    if brightness_detected or motion_detected:
        presence_detected = True
    previous_distance = distance
    #print("Presence detected: ", presence_detected)
    #print("The distance from object is ", distance, "cm")
    #print("The brightness is ", brightness)
    return presence_detected

def draw_rotary_encoder(rotary_counter):
    circle_radius = 20
    centre_x = 100
    centre_y = 39
    oled.fill_rect(80, 13, 128, 64, 0)
    angle = rotary_counter * micropython.const(2 * math.pi / 20)
    # draw the circle
    oled.ellipse(centre_x, centre_y, circle_radius, circle_radius, 1)
    # draw the deadzone
    inner_radius = 15
    for a in deadzone, -deadzone:
        outer_x = round(centre_x + circle_radius * math.sin(a))
        outer_y = round(centre_y - circle_radius * math.cos(a))
        inner_x = round(centre_x + inner_radius * math.sin(a))
        inner_y = round(centre_y - inner_radius * math.cos(a))
        oled.line(inner_x, inner_y, outer_x, outer_y, 1)
    # draw the dial
    dial_x = round(centre_x + circle_radius * math.sin(angle))
    dial_y = round(centre_y - circle_radius * math.cos(angle))
    oled.line(centre_x, centre_y, dial_x, dial_y, 1)
    # if outside the deadzone, draw a "progress bar" following the dial, and some text
    if angle > deadzone:
        deadzone_deg = round(math.degrees(deadzone))
        angle_deg = round(math.degrees(angle))
        for deg in range(deadzone_deg, angle_deg+1):
            a = math.radians(deg)
            outer_x = round(centre_x + circle_radius * math.sin(a))
            outer_y = round(centre_y - circle_radius * math.cos(a))
            inner_x = round(centre_x + inner_radius * math.sin(a))
            inner_y = round(centre_y - inner_radius * math.cos(a))
            oled.line(inner_x, inner_y, outer_x, outer_y, 1)
        oled.fill_rect(0, 48, 75, 64, 0)
        oled.fill_rect(10, 48, 60, 16, 1)
        write12.text("Extending", 20, 49, bgcolor=1, color=0)
    elif angle < -deadzone:
        deadzone_deg = round(math.degrees(deadzone))
        angle_deg = round(math.degrees(angle))
        for deg in range(-deadzone_deg, angle_deg-1, -1):
            a = math.radians(deg)
            outer_x = round(centre_x + circle_radius * math.sin(a))
            outer_y = round(centre_y - circle_radius * math.cos(a))
            inner_x = round(centre_x + inner_radius * math.sin(a))
            inner_y = round(centre_y - inner_radius * math.cos(a))
            oled.line(inner_x, inner_y, outer_x, outer_y, 1)
        oled.fill_rect(0, 48, 75, 64, 0)
        oled.fill_rect(10, 48, 60, 16, 1)
        write12.text("Retracting", 18, 49, bgcolor=1, color=0)
    else:
        if action_in_progress: # automatic retract when switching from MANUAL mode to DEBUG mode should show "Retracting"
            oled.fill_rect(0, 48, 75, 64, 0)
            oled.fill_rect(10, 48, 60, 16, 1)
            write12.text("Retracting", 18, 49, bgcolor=1, color=0)
        else:
            oled.fill_rect(0, 48, 75, 64, 0)
            oled.rect(10, 48, 60, 16, 1)
            write12.text("Motor off", 20, 49, 1)

def draw_status_bar(): # display stuff at the top of the oled screen
    oled.fill_rect(0, 0, 128, 15, 0)
    battery_percentage = measure_battery()
    select_battery_icon = get_battery_icon(battery_percentage)
    battery.text(select_battery_icon, 108, -1)
    # DEBUG mode shows sensor output
    if mode_debug and not mode_manual:
        brightness = round(measure_brightness())
        write12.text(str(brightness) + "%", 15, 0)
        lightbulb.char('lightbulb', 0, 0)
        distance = round(measure_distance())
        write12.text(str(distance) + "cm", 63, 0)
        arrows.char('arrows-alt-h', 45, 0)

def draw_toilet(frame=1):
    oled.fill_rect(80, 13, 128, 64, 0)
    oled.blit(toilet_icon, 80, 12)
    if frame == 1:
        oled.rect(105, 15, 3, 22, 1)
    elif frame == 2:
        oled.line(105, 35, 120, 20, 1)
        oled.line(107, 36, 122, 21, 1)
        oled.pixel(106, 35, 1)
        oled.pixel(121, 20, 1)
    elif frame == 3:
        oled.rect(105, 34, 22, 3, 1)

def get_battery_icon(battery_percentage):
    # based on table at https://blog.ampow.com/lipo-voltage-chart/
    if battery_percentage >= 90:
        select_battery_icon = str(5)
    elif battery_percentage >= 70:
        select_battery_icon = str(4)
    elif battery_percentage >= 50:
        select_battery_icon = str(3)
    elif battery_percentage >= 30:
        select_battery_icon = str(2)
    else:
        select_battery_icon = str(1)
    return select_battery_icon

battery_measurements = [50, 50, 50, 50, 50]
def measure_battery():
    global battery_measurements
    battery_voltage = pin_battery_adc.read_u16() * voltage_conversion_factor + voltage_correction_factor
    # Use curve-fitting to get battery percentage (see graph included in Images folder)
    battery_percentage = 39.3*battery_voltage**3 - 1431.53*battery_voltage**2 + 17415*battery_voltage - 70673
    battery_measurements.append(battery_percentage)
    battery_measurements.pop(0)
    battery_percentage_mean = sum(battery_measurements)/len(battery_measurements)
    return battery_percentage_mean

def test_battery():
    while True:
        battery_percentage = measure_battery()
        print(battery_measurements)
        print("Battery %: ", battery_percentage)
        utime.sleep(2)

def measure_brightness():
    brightness = pin_sfh300_adc.read_u16() * 0.00152590218 # 100%/65535 = 0.00152590218
    return(brightness)

def measure_distance():
    pin_hcsr04_trigger.low()
    utime.sleep_us(2)
    pin_hcsr04_trigger.high()
    utime.sleep_us(5)
    pin_hcsr04_trigger.low()
    while pin_hcsr04_echo.value() == 0:
        signaloff = utime.ticks_us()
    while pin_hcsr04_echo.value() == 1:
        signalon = utime.ticks_us()
    timepassed = utime.ticks_diff(signalon, signaloff)
    distance = timepassed * 0.01715 # (0.0343 cm per us)/2 = 0.01715
    #print("The distance from object is ", distance, "cm")
    return(distance)

def motor_cleanup():
    for pin in range(0, len(motor_pins)):
        motor_pins[pin].low()

def motor_spin(revolutions=1, step_sleep=step_sleep_retract):
    gc.collect()
    global action_in_progress, motor_cancel, motor_retract_revolutions
    motor_cancel = False
    motor_retract_revolutions = 0
    i = 0
    motor_step_counter = 0
    motor_cleanup()
    for i in range(revolutions*steps_per_revolution):
        for pin in range(0, len(motor_pins)):
            motor_pins[pin].value(step_sequence[motor_step_counter][pin])
        if motor_direction==True:
            motor_step_counter = (motor_step_counter - 1) % 4
        elif motor_direction==False:
            motor_step_counter = (motor_step_counter + 1) % 4
        if motor_cancel:
            #irq_state = machine.disable_irq()
            break
        utime.sleep(step_sleep)
    motor_cleanup()
    # If action is ongoing when switching into DEBUG mode, rotating the encoder cancels the action
    if mode_debug and motor_cancel and rotary_counter != 0:
        motor_retract_revolutions = 0
    elif motor_direction == False:
        motor_retract_revolutions = i/steps_per_revolution
    elif motor_direction == True:
        motor_retract_revolutions = revolutions - i/steps_per_revolution
    if motor_retract_revolutions < 0.001: # 16 bit machine epsilon rounding produces 4.88e-04
        motor_retract_revolutions = 0
    if motor_cancel:
        motor_cancel = False
        #machine.enable_irq(irq_state)
    action_in_progress = False
    #_thread.exit()
    
def motor_spin_debug(step_sleep=step_sleep_retract):
    gc.collect()
    global action_in_progress
    motor_step_counter = 0
    motor_cleanup()
    while abs(rotary_counter * micropython.const(2 * math.pi / 20)) > deadzone:
        for pin in range(0, len(motor_pins)):
            motor_pins[pin].value(step_sequence[motor_step_counter][pin])
        if motor_direction==True:
            motor_step_counter = (motor_step_counter - 1) % 4
        elif motor_direction==False:
            motor_step_counter = (motor_step_counter + 1) % 4
        utime.sleep(step_sleep)
    motor_cleanup()
    action_in_progress = False
    #_thread.exit()
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

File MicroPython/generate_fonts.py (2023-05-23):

from oled.fonts import gen

# Generate fonts in the regular python interpreter (not micropython), because the pygame package is required.
# Guide here: https://espresso-ide.readthedocs.io/projects/micropython-oled/en/latest/content/getting_started.html
# I had to comment out "from machine import..." in lazy.py

# lightbulb icons
# Sadly "lightbulb-on" is a premium icon
characters = {'lightbulb': '\uf0eb'}
font = gen.generate_oled_font("Font Awesome 6 Free, Regular", 15, characters)
#print(font)

# battery status icons
characters = {'1': '\uf244',
              '2': '\uf243',
              '3': '\uf242',
              '4': "\uf241",
              '5': "\uf240",
             }
font = gen.generate_oled_font("Font Awesome 6 Free, Solid", 17, characters)
#print(font)

# ruler icon
characters = {'ruler': '\uf545'}
font = gen.generate_oled_font("Font Awesome 6 Free, Regular", 15, characters)
#print(font)

# horizontal arrows icon (maybe looks better than ruler)
characters = {'arrows-alt-h': '\uf337'}
font = gen.generate_oled_font("Font Awesome 6 Free, Regular", 15, characters)
#print(font)

# toilet icon (frontal)
characters = {'toilet': '\uf7d8'}
font = gen.generate_oled_font("Font Awesome 6 Free, Regular", 17, characters)
#print(font)

characters = {'smile': '\uf118'}
font = gen.generate_oled_font("Font Awesome 6 Free, Regular", 17, characters)
print(font)

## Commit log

2023-04-10 Added a first draft of the BoM to the readme
2023-04-10 Updated the readme BoM
2023-04-10 Added DC-DC stepdown module to readme BoM
2023-04-10 Updated readme BoM
2023-04-15 Updated BoM in readme
2023-05-13 mode switching works, also added button debounce
2023-05-14 added battery icon
2023-05-16 added CAD files
    [Gearbox_Cover.stl, HC-SR04.stl, Hole_Size_Gauge.STL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]
2023-05-17 started experimenting with uasyncio threading
2023-05-18 started getting the rotary encoder to encode rotation
2023-05-18 the rotary encoder is now encoding rotation
2023-05-19 added motor status to debug screen
2023-05-19 continued work on state machine, when switching from MANUAL to DEBUG mode
2023-05-19 debug mode motor retract is working, but interrupting the retract causes system to completely freeze, investigation needed
2023-05-19 threading + interrupt still produces freeze, may need to reconsider polling...
2023-05-20 freezing is now slightly less common, because the motor thread shutdown signal is sent from the interrupt itself, but freezing still occurs, maybe due to shared resources being manipulated concurrent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
2023-05-20 freezing issue seems mostly resolved by adding hard=True in pin.irq()
    [main.py]
2023-05-20 implemented motor rotation in debug mode
2023-05-20 removed wake option from button interrupt
2023-05-20 fixes regarding motor direction, and stopping motor when switching from DEBUG to AUTO mode
    [main.py]
2023-05-20 added fritzing breadboard image, and started working on AUTO and MANUAL motor control
2023-05-21 state machine mostly working, unhandled edge case when button pushed during AUTO closing action
2023-05-21 started working on battery measurement function, also added picture explaining polynomial used in measure_battery()
2023-05-21 updated battery graph image
2023-05-21 Update BoM in readme
2023-05-21 implemented rolling average for battery measurement
2023-05-22 started working on battery ADC callibration
2023-05-23 switching from AUTO to MANUAL mode while action is ongoing is now handled correctly
    [generate_fonts.py, main.py]
2023-05-23 corrected error in voltage graph, minor tweaks in CAD, minor cleanup in python
    [backplate.scad, breadboard_mounting_bracket.scad]
2023-05-24 added STL files
    [axle.stl, backplate.scad, backplate.stl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]
2023-05-26 Made the axle a bit slimmer, because the tolerances are too tight, and there is too much friction with the axle mounts and the main gear
    [axle.scad, axle.stl, backplate.scad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]
2023-06-04 made new sun/planet gears for the epicyclic gearbox, the original ones were too tight/too much friction
    [gears.scad, generate_stl_files.scad, planet_gear.stl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]
2023-06-05 combined the front_axle_mount and ring_gear_base_mount into one component: ring_gear_and_front_axle_mount, also other small CAD adjustments
    [axle.scad, axle.stl, backplate.scad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]
2023-06-08 added m4 standoffs, updated BoM, minor tweaks
    [axle.stl, backplate.stl, generate_stl_files.scad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]
2023-06-09 updated circuit/breadboard diagrams, and callibrated variables in main.py
    [axle.scad, axle.stl]
2023-06-10 cleanup of code, removed print() used for debugging
2023-06-19 tweaked battery monitoring code, and other minor fixes
    [main.py]
2023-06-19 finished battery monitor tweaking (for now)
2023-06-19 tweaked voltage_correction_factor
2023-07-03 minor battery measurement callibration
2023-07-21 tweaked bettery callibration, improved battery life by using lightsleep instead of sleep
